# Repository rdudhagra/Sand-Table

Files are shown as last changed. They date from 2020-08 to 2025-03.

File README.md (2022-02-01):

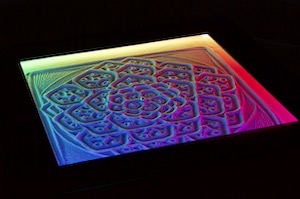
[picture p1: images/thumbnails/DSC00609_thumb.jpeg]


# Sand Table
  

### An open-source platform for building DIY sand tables (like the Sisyphus or ZenXY)
### Designed by Ravi Dudhagra ([@rdudhagra](https://github.com/rdudhagra))
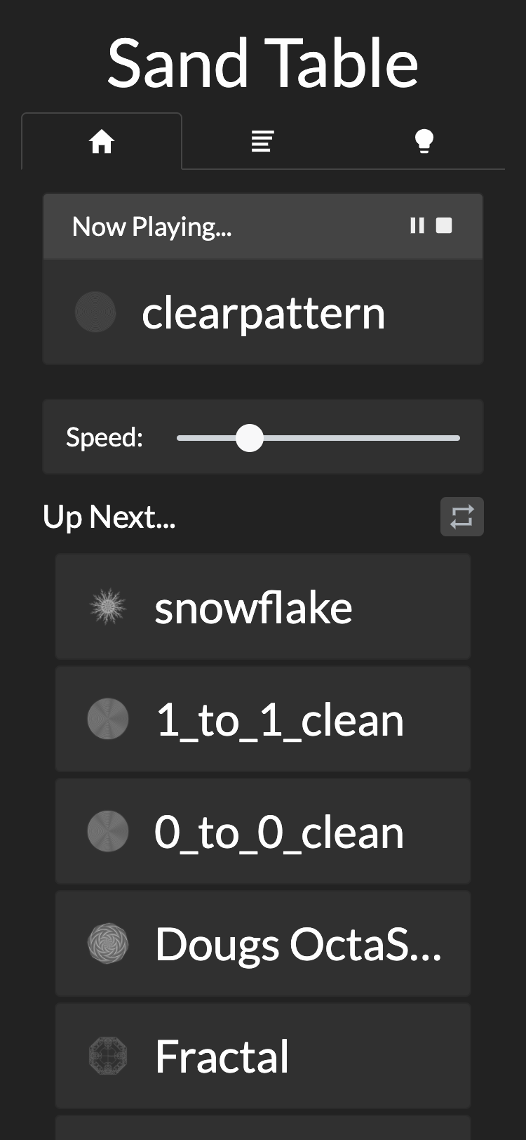
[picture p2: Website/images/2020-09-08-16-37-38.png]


Inspired by Bruce Shapiro's [Sisyphus Tables](https://sisyphus-industries.com/), I created my own DIY sand table that uses a CoreXY system to create a square-shaped canvas, yet is still fully compatible with Sisyphus Table `.thr` files. 

The table is built out of half-inch plywood and some 1x8 pine boards, glued/nailed together, and painted glossy black. The CoreXY system is built out of OpenBuilds V-Slot rail and 3D-printed parts. Use of Trinamic's TMC2209 stepper drivers means quiet movement and sensor-less homing, further simplifying the electronics under the hood. The table can be controlled directly from your smartphone thanks to a webserver that runs on an onboard Raspberry Pi. This table makes an extremely fun and rewarding project that will last a lifetime, and should cost less than $750.

See the `Build Guide` folder for instructions on my specific build, or visit the other folders for direct access to the software. Check out the `discussions` tab for other helpful info/troubleshooting advice.

> Check out [@SeanTurner71](https://github.com/SeanTurner71)'s [build video](https://www.youtube.com/watch?v=QCLmVpVkmQY) for an overview of the assembly process and some mesmerizing timelapses!

<br>

| | | |
| :---: | :---: | :---: |
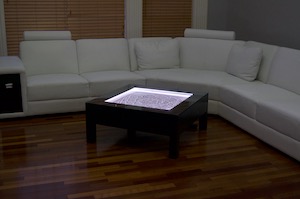
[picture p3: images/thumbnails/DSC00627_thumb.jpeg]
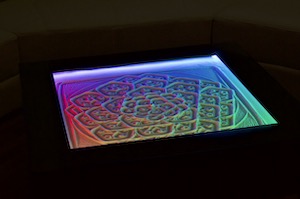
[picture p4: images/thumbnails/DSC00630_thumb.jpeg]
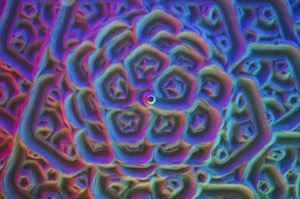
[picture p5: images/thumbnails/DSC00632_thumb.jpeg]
|  |  |  |
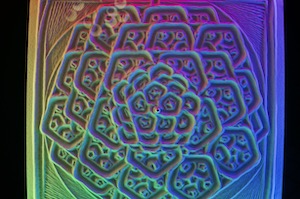
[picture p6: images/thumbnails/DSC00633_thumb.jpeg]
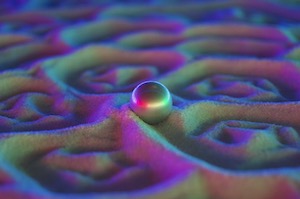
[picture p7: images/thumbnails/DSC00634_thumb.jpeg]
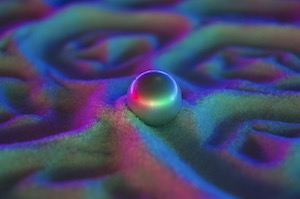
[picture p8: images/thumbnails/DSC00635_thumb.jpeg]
|  |  |  |
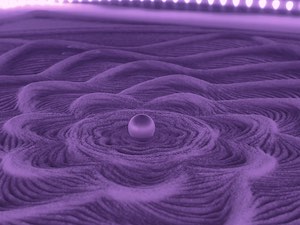
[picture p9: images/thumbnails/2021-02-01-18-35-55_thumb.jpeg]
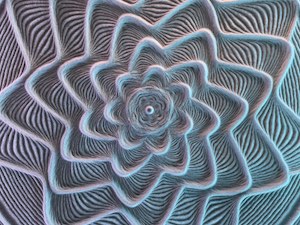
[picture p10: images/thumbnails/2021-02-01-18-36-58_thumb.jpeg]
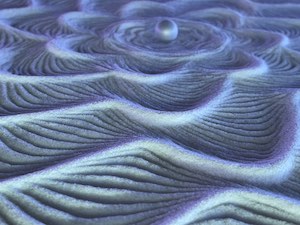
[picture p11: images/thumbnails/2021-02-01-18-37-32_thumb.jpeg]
|  |  |  |
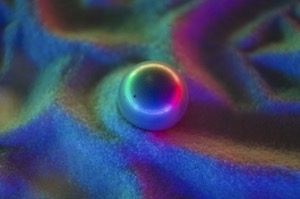
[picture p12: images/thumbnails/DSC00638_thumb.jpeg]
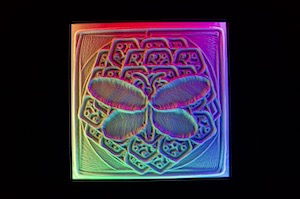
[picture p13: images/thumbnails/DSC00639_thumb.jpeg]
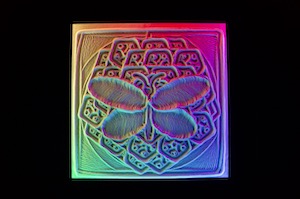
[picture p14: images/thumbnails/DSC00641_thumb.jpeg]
|  |  |  |
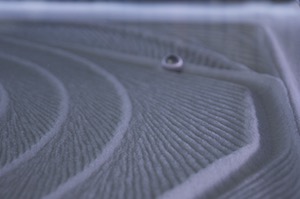
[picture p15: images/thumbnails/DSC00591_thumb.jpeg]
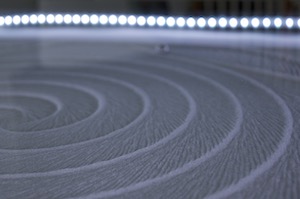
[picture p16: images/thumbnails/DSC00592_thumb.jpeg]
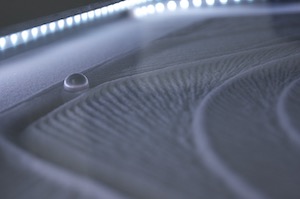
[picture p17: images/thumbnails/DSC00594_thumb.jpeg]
|  |  |  |
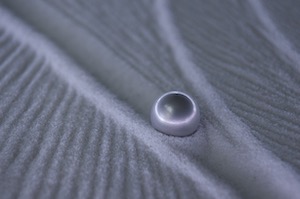
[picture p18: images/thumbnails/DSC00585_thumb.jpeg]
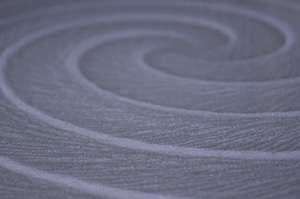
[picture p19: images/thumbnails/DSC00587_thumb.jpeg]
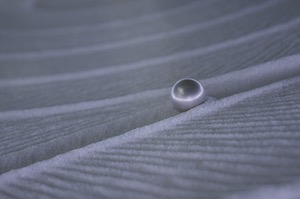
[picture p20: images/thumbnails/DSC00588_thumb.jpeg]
|  |  |  |
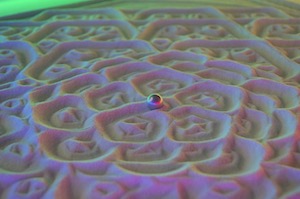
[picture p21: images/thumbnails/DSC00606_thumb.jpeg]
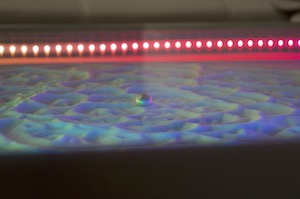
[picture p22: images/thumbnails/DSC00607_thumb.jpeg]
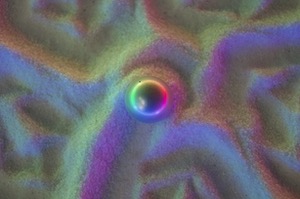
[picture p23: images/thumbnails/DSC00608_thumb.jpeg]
|  |  |  |
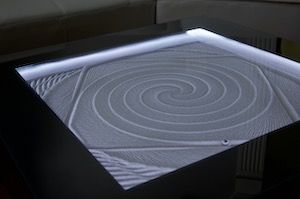
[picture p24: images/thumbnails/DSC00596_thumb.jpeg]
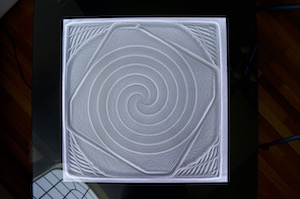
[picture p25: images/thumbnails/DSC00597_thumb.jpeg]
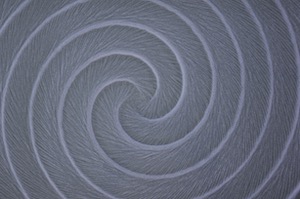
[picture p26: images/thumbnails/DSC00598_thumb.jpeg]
|  |  |  |
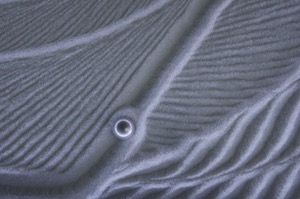
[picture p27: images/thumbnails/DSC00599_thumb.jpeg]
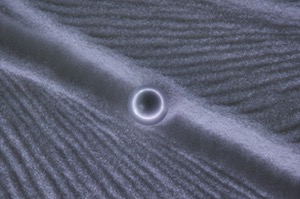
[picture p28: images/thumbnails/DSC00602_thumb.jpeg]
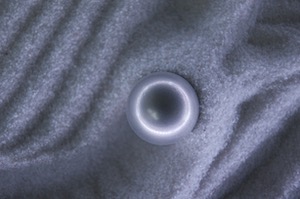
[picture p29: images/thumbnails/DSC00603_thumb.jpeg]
|  |  |  |
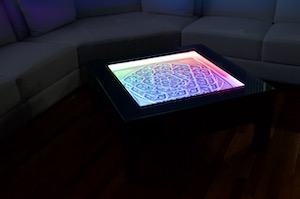
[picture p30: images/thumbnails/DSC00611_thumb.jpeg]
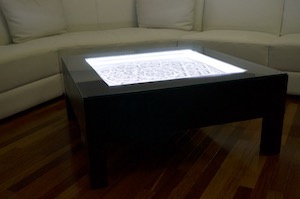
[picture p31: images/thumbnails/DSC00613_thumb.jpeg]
|  |  |  |
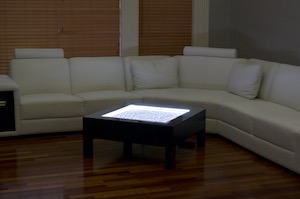
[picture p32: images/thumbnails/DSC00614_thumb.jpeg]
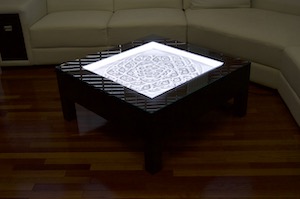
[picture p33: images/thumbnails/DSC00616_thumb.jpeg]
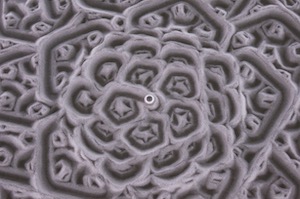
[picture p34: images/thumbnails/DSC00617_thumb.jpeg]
|  |  |  |
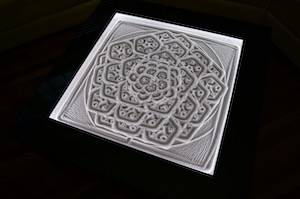
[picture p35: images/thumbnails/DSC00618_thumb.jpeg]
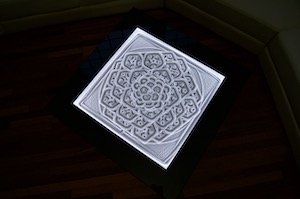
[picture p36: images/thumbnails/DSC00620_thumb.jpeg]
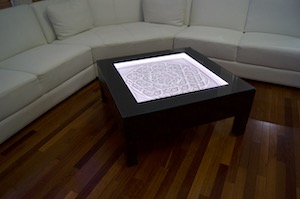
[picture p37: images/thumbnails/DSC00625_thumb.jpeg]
|  |  |  |

More pictures in the `images` folder...

<a href="https://trackgit.com">
trackgit-views
</a>

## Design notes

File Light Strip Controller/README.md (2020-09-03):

# Light Strip Controller
### An Arduino program meant for controlling an RGB LED strip using FastLED, with predefined modes and the ability to be controlled through serial
### Designed by Ravi Dudhagra ([@rdudhagra](https://github.com/rdudhagra))

## Prerequisites
Hardware:
- Arduino (literally anything that FastLED can run on...I used an Uno)
- LED Strip(s) (anything FastLED can support), and an adequate way to power them
  - Note: because of how the code was optimized to use 8-bit arithmetic (because it's orders of magnitude faster than floating-point math), this code supports **at most 255 led's**. If you want more led's, you will have to convert the 8-bit math to 16-bit/floating point arithmetic, which in that case, I would recommend using a more powerful arduino like a Due/Teensy.

## Configuration
All configuration is done in `main/constants.h`. The most important parameter is `NUM_LEDS`, which controls how many led's that the software will compute values for. 

Also important is the `DATA_PIN` parameter, which controls what pin on the Arduino will send the data to the led's. If you are using an led strip with more than one data pin (such as a DotStar), you may have to modify this file, as well as `main.ino`. 

Note that changing `FRAMES_PER_SECOND` will speed up/slow down the patterns themselves as well. 

Change `MAX_MILLIAMPS` to whatever the maximum current rating of your power source is to avoid blowing stuff up. 

The rest of the parameters control the individual modes...these can be left as is unless you're curious...

## Installing

Using the Arduino IDE (or vscode extension, etc.), upload the firmware to your Arduino. You can then use the sand table webserver to test it, or use the file `util/serial_send.py` to manually send commands.

## Development

### Creating custom modes

To create a new mode, several things must be done:
1. In `constants.h`, assign a new number to the color mode. The new number must count up from the other modes to work with the webserver (so if modes 0,1,2,3,4,5,6 are set to something, the next mode number must be 7).
2. Create a new file for your mode. Each mode contains two functions: an init function, that returns a new uint8_t* (can be used to store data about each frame like a counter, etc.), and an update function, that runs once per frame and has access to to the data pointer. See the other modes for an example.
3. In `mode.h`, update both switch statements with the new mode you just created and the functions from the new file you just created.
4. In `Website/src/app/components/Led.jsx`, add the new mode to the list `this.modes`.

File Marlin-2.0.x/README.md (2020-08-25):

# Sand Table - Customized Marlin Firmware

This is the build of Marlin that I used for my sand table build. The only modifications from stock marlin are in `configuration.h` and `configuration_adv.h`. Most of the changes fall in two categories:
- Changes everyone makes, like the dimensions of the table, steps per mm, etc.
- TMC2209-specific settings, such as microstepping and sensorless homing setup

If your sand table follows my setup exactly, this firmware should work out of the box. However, if you make modifications or want to use a newer version of Marlin, making the changes yourself should be fairly simple. Just look for a guide on setting up Marlin for a 3D-printer (but there's no z-axis or extruder, so that gets rid of 90% of the setup), and a guide for setting up the specific stepper driver you plan on using.

<br />

---

<br />
<br />
<br />

# Marlin 3D Printer Firmware






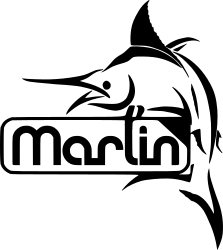
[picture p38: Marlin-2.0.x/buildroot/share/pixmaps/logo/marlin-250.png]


Additional documentation can be found at the [Marlin Home Page](http://marlinfw.org/).
Please let us know if Marlin misbehaves in any way. Volunteers are standing by!

## Marlin 2.0

Marlin 2.0 takes this popular RepRap firmware to the next level by adding support for much faster 32-bit and ARM-based boards while improving support for 8-bit AVR boards. Read about Marlin's decision to use a "Hardware Abstraction Layer" below.

Download earlier versions of Marlin on the [Releases page](https://github.com/MarlinFirmware/Marlin/releases).

## Building Marlin 2.0

To build Marlin 2.0 you'll need [Arduino IDE 1.8.8 or newer](https://www.arduino.cc/en/main/software) or [PlatformIO](http://docs.platformio.org/en/latest/ide.html#platformio-ide). Detailed build and install instructions are posted at:

  - [Installing Marlin (Arduino)](http://marlinfw.org/docs/basics/install_arduino.html)
  - [Installing Marlin (VSCode)](http://marlinfw.org/docs/basics/install_platformio_vscode.html).

### Supported Platforms

  Platform|MCU|Example Boards
  --------|---|-------
  [Arduino AVR](https://www.arduino.cc/)|ATmega|RAMPS, Melzi, RAMBo
  [Teensy++ 2.0](http://www.microchip.com/wwwproducts/en/AT90USB1286)|AT90USB1286|Printrboard
  [Arduino Due](https://www.arduino.cc/en/Guide/ArduinoDue)|SAM3X8E|RAMPS-FD, RADDS, RAMPS4DUE
  [LPC1768](http://www.nxp.com/products/microcontrollers-and-processors/arm-based-processors-and-mcus/lpc-cortex-m-mcus/lpc1700-cortex-m3/512kb-flash-64kb-sram-ethernet-usb-lqfp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)|ARM® Cortex-M3|MKS SBASE, Re-ARM, Selena Compact
  [LPC1769](https://www.nxp.com/products/processors-and-microcontrollers/arm-microcontrollers/general-purpose-mcus/lpc1700-cortex-m3/512kb-flash-64kb-sram-ethernet-usb-lqfp100-p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)|ARM® Cortex-M3|Smoothieboard, Azteeg X5 mini, TH3D EZBoard
  [STM32F103](https://www.st.com/en/microcontrollers-microprocessors/stm32f103.html)|ARM® Cortex-M3|Malyan M200, GTM32 Pro, MKS Robin, BTT SKR Mini
  [STM32F401](https://www.st.com/en/microcontrollers-microprocessors/stm32f401.html)|ARM® Cortex-M4|ARMED, Rumba32, SKR Pro, Lerdge, FYSETC S6
  [STM32F7x6](https://www.st.com/en/microcontrollers-microprocessors/stm32f7x6.html)|ARM® Cortex-M7|The Borg, RemRam V1
  [SAMD51P20A](https://www.adafruit.com/product/4064)|ARM® Cortex-M4|Adafruit Grand Central M4
  [Teensy 3.5](https://www.pjrc.com/store/teensy35.html)|ARM® Cortex-M4|
  [Teensy 3.6](https://www.pjrc.com/store/teensy36.html)|ARM® Cortex-M4|

## Submitting Changes

- Submit **Bug Fixes** as Pull Requests to the ([bugfix-2.0.x](https://github.com/MarlinFirmware/Marlin/tree/bugfix-2.0.x)) branch.
- Follow the [Coding Standards](http://marlinfw.org/docs/development/coding_standards.html) to gain points with the maintainers.
- Please submit your questions and concerns to the [Issue Queue](https://github.com/MarlinFirmware/Marlin/issues).

## Marlin Support

For best results getting help with configuration and troubleshooting, please use the following resources:

- [Marlin Documentation](http://marlinfw.org) - Official Marlin documentation
- [Marlin Discord](https://discord.gg/n5NJ59y) - Discuss issues with Marlin users and developers
- Facebook Group ["Marlin Firmware"](https://www.facebook.com/groups/1049718498464482/)
- RepRap.org [Marlin Forum](http://forums.reprap.org/list.php?415)
- [Tom's 3D Forums](https://discuss.toms3d.org/)
- Facebook Group ["Marlin Firmware for 3D Printers"](https://www.facebook.com/groups/3Dtechtalk/)
- [Marlin Configuration](https://www.youtube.com/results?search_query=marlin+configuration) on YouTube

## Credits

The current Marlin dev team consists of:

 - Scott Lahteine [[@thinkyhead](https://github.com/thinkyhead)] - USA &nbsp; [Donate](http://www.thinkyhead.com/donate-to-marlin) / Flattr: 
 - Roxanne Neufeld [[@Roxy-3D](https://github.com/Roxy-3D)] - USA
 - Chris Pepper [[@p3p](https://github.com/p3p)] - UK
 - Bob Kuhn [[@Bob-the-Kuhn](https://github.com/Bob-the-Kuhn)] - USA
 - João Brazio [[@jbrazio](https://github.com/jbrazio)] - Portugal
 - Erik van der Zalm [[@ErikZalm](https://github.com/ErikZalm)] - Netherlands &nbsp; 

## License

Marlin is published under the [GPL license](/LICENSE) because we believe in open development. The GPL comes with both rights and obligations. Whether you use Marlin firmware as the driver for your open or closed-source product, you must keep Marlin open, and you must provide your compatible Marlin source code to end users upon request. The most straightforward way to comply with the Marlin license is to make a fork of Marlin on Github, perform your modifications, and direct users to your modified fork.

While we can't prevent the use of this code in products (3D printers, CNC, etc.) that are closed source or crippled by a patent, we would prefer that you choose another firmware or, better yet, make your own.

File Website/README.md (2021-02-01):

<h1>Webserver</h1>
<h3>A NodeJS webserver with ReactJS and Bootstrap for controlling your sand table remotely</h3>

Designed by Ravi Dudhagra ([@rdudhagra](https://github.com/rdudhagra))

- [Installation Instructions](#installation-instructions)
  - [Prerequisites](#prerequisites)
  - [Building](#building)
  - [Running the webserver](#running-the-webserver)
  - [Running the webserver (development)](#running-the-webserver-development)
- [Downloading tracks](#downloading-tracks)
- [Screenshots](#screenshots)

# Installation Instructions

## Prerequisites
This project was developed with the following:
- `NodeJS v13.11.0`
- `NPM v6.14.5`

## Building
1. Download this folder to the directory of choice
2. In the same directory as `package.json`, run
   ```bash
   npm install # installs packages and dependencies
   ```
3. In the file `.env`, edit the parameters to match your setup

## Running the webserver
1. In the same directory as `package.json`, run
   ```bash
   npm run prod # compiles client and server files in production mode, and runs server
   ```
2. Visit `http://[ip address of machine]` in a web browser (runs on port 80)

If you want to run this webserver through systemd, the script `start.sh` should assist in this, assuming you're using NVM to manage Node versions.

## Running the webserver (development)
1. In the same directory as `package.json`, run
   ```bash
   npm start # compiles client files, compiles server files in memory, starts server with nodemon (restarts on file changes)
   ```
2. Visit `http://[ip address of machine]:3000` in a web browser (runs on port 3000)

# Downloading tracks
Any `.thr` file compatible with the Sisyphus table will work with this software. A collection of publicly available tracks can be found at the following links:
- https://github.com/Dithermaster/sisyphus
- https://github.com/SlightlyLoony/JSisyphus
- https://github.com/heropup/sisyphus
- http://thejuggler.net/sisyphus/
- https://github.com/ddkengr/Sisyphus-threads

# Screenshots

| | | |
| :---: | :---: | :---: |
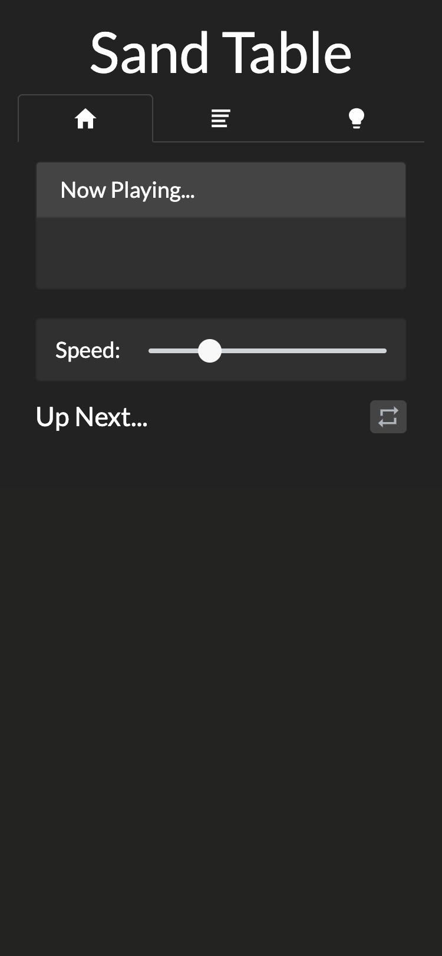
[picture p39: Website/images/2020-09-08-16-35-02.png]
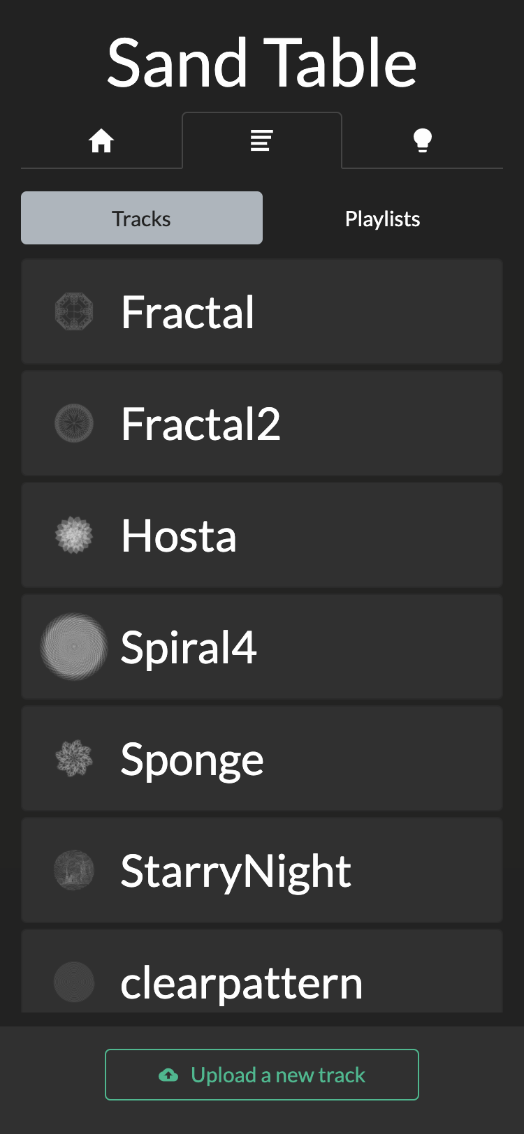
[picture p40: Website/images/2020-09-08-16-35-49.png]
|  |  |  |
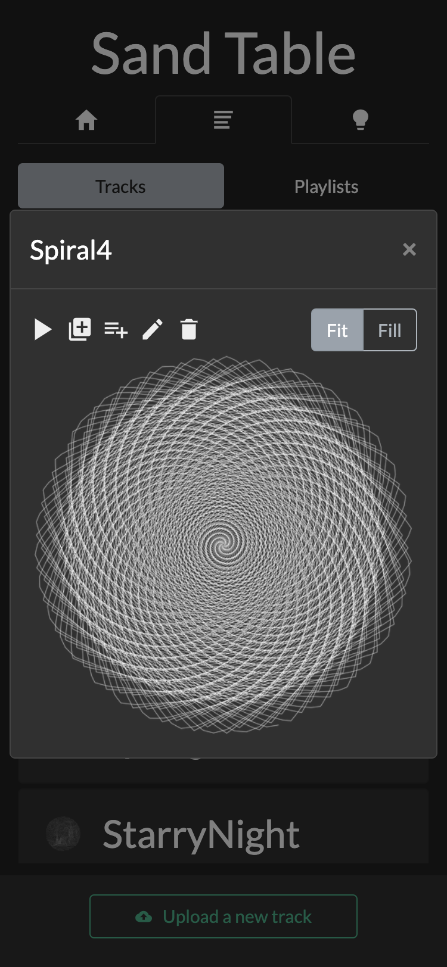
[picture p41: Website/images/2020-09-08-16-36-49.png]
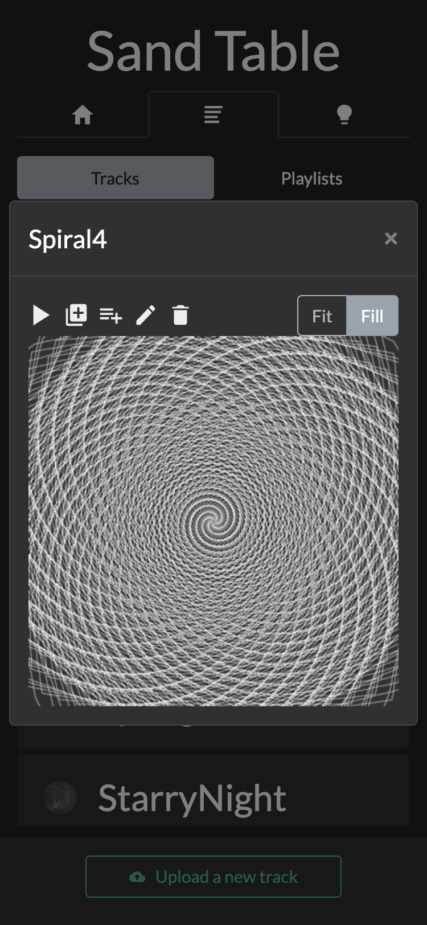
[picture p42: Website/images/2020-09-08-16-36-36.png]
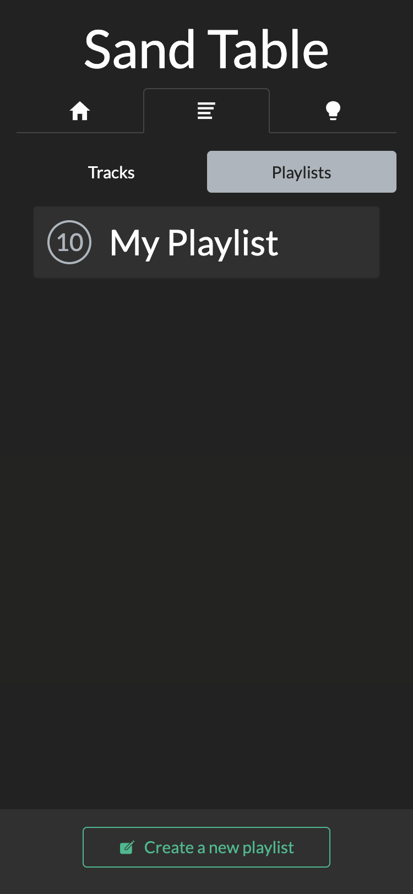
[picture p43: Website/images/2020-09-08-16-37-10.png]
|  |  |  |
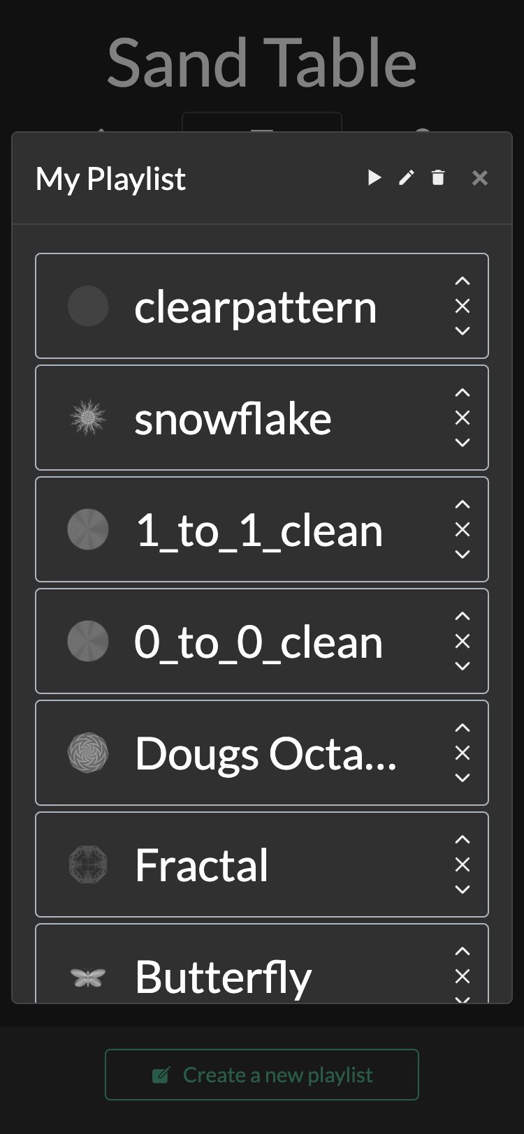
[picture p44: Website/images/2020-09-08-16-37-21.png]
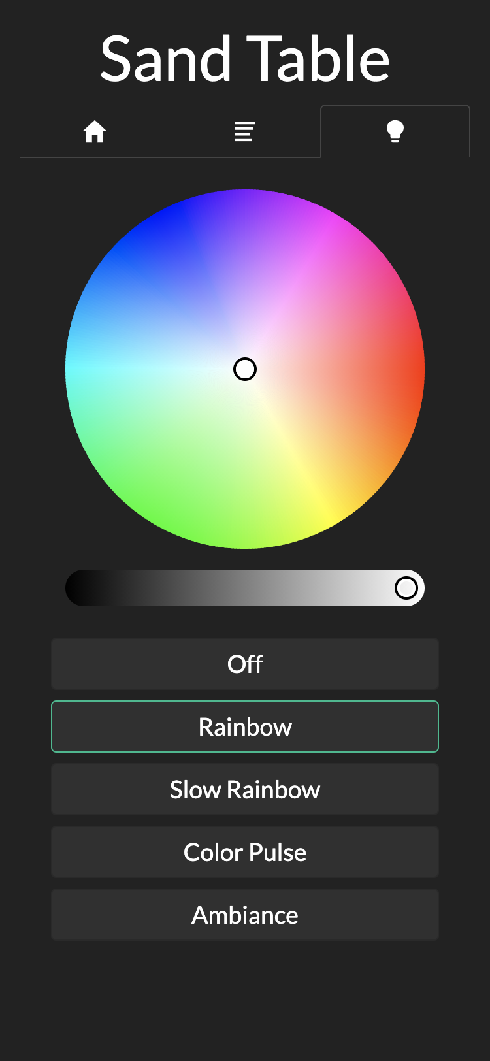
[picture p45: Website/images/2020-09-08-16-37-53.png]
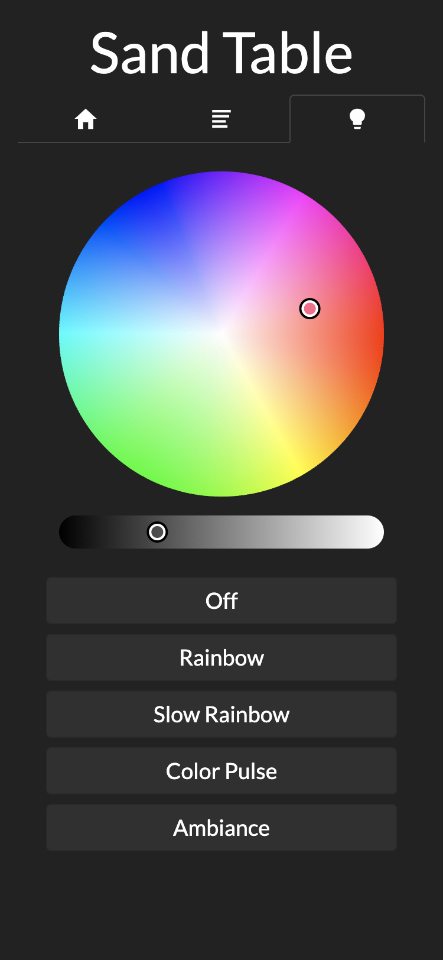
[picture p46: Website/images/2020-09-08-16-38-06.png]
|  |  |  |

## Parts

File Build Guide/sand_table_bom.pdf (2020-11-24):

Item | Link | Price | Quantity | Total | Remarks
| 1x8 pine board (8'), square edges | https://www.homedepot.com/p/1-in-x-8-in-x-8-ft-Select-Pine-Board-929612/202535862 $ | 22.22 | 2 | $ 44.44 | If you have proper woodworking tools, you could probably get away with lower-quality boards
| 1/2" sanded plywood, 4'x8' | https:/ /www.homedepot.com/ p/ 12mm-Sande-Plywood-1-2-in-Category-x-4-ft-x-8-ft-Actual-0-472-in-x-48-in-x-96-in-454532/ 203414055 | $ 35.95 | 1 | $ 35.95
| 5.0mm underlayment plywood, 4'x4' | https:/ /www.homedepot.com/ p/Tri-PLY-U nderlayment-Common-5-0-mm-x-4-ft-x-4-ft-Actual-0-196-in-x-47-75-in-x-48-in-448887/ 202327787 | $ 10.48 | 1 | $ 10.48 | Any thin wood will work, this is a pretty economical choice
| Finishing nails | https://www.homedepot.com/p/Grip-Rite-13-x-2-in-6-Penny-Bright-Steel-Finish-Nails-1-lb-Pack-6F1/100027781 | $ 4.75 | 1 | $ 4.75
| Gray spray paint primer | https:/ /www.homedepot.com/ p/ Rus t-Oleum-Painter-s -Touch-2X-12-oz -Flat-G ray-Primer-General-Purpose-Spray-Paint-334017/ 307244825 | $ 3.98 | 6 | $ 23.88 | You'll need more than you think
| Gloss black spray paint | https://www.homedepot.com/p/Rust-Oleum-Painter-s-Touch-2X -12 -oz-Gloss-Black-General-Purpose-Spray-Paint-334026/307244831 | $ 3.98 | 4 | $ 15.92 | These are probably not the best options…but choose whatever you need for the finish that you want to achieve
| Clear coat spray paint | https://www.homedepot.com/p/Rust-Oleum-Painter-s-Touch-2X -12 -oz-Gloss-Clear-General-Purpose-Spray-Paint-334029/307244797 | $ 3.98 | 1 | $ 3.98 | Makes the finish slightly less glossy, but improves durability
| M8 Nuts | https://www.homedepot.com/p/Everbilt-M8-10-9-Zinc-Metric-Hex-Nut-5-per-Bag-802418/204281770 | $ 2.27 | 1 | $ 2.27 | For use with the IKEA legs
M8 Washers | https://www.homedepot.com/p/Everbilt-M8-Zinc -Plated-Metric -Flat-Washer-5-Piece-Bag-802458/204604800 | $ 0.97 | 1 | $ 0.97 | Or whatever you can find in your spare parts drawer that's close enough
BRENNÅSEN bed legs (IKEA) | https://www.ikea.com/us/en/p/brennasen-leg-black-stained-00299689/ | $ 30.00 | 1 | $ 30.00 | Not always in stock, but alternatives either have long shipping times or are pricey (or you could make your own legs…)
36"x36" Glass table top (1/4" thick) | h ttp s://www.amazo n .co m/Sq u are-Glass-Tab le-Th ick-P o li sh ed /d p /B 0 0 1 E6 C ZKW /ref=sr_1 _7 ?crid =2 R ZX DC HGC K 6 X 5 &d ch ild =1 &keywo rd s=3 6 x3 6 +glass+tab le+to p &q id =1 5 9 8 9 0 2 6 4 3 &sp refix=3 6 x3 6 +glass+tab le%2 C ap s%2 C 1 3 7 &sr=8 -7 | $ 99.95 | 1 | $ 99.95 | You should check the availability of local glass suppliers in your area for a better deal (I purchased mine for around $60)
| 3D Printer Filament (PLA) | https://www.amazon.com/HATCHBOX-3D-Filament-Dimensional-Accuracy/dp/B00J0ECR5I?ref_=ast_sto_dp | $ 22.99 | 1 | $ 22.99 | Whatever you have will work, but you'll need the majority of the spool for all the parts. If you can print with something stronger like PETG, that's better.
| Stepper motor dampers | https://www.amazon.com/gp/product/B07GWN6V89/ref=ppx_yo_dt_b_asin_title_o08_s00?ie=UTF8&psc=1 | $ 13.99 | 1 | $ 13.99 | Not required, but greatly reduce noise
| M5 Square nuts | https://www.amazon.com/gp/product/B01HSKL7Z6/ref=ppx_yo_dt_b_asin_title_o03_s00?ie=UTF8&psc=1 | $ 8.09 | 1 | $ 8.09 | You won't need this many
| 12V to 5V step-down, 15A max | https://www.amazon.com/gp/product/B07V7YY5X6/ref=ppx_yo_dt_b_asin_title_o05_s00?ie=UTF8&psc=1 | $ 13.95 | 1 | $ 13.95
| M5 10mm bolts | https://www.amazon.com/gp/product/B07KWQ4JFK/ref=ppx_yo_dt_b_search_asin_title?ie=UTF8&psc=1 | $ 8.49 | 1 | $ 8.49
| M5 40mm bolts | https://www.amazon.com/gp/product/B083F9MVWT/ref=ppx_yo_dt_b_asin_title_o07_s00?ie=UTF8&psc=1 | $ 8.99 | 1 | $ 8.99
| TMC2209 Stepper drivers | https://www.amazon.com/gp/product/B07W5S3KVF/ref=ppx_yo_dt_b_asin_title_o07_s02?ie=UTF8&psc=1 | $ 29.98 | 1 | $ 29.98 | You only need two, this comes with four
| 1 kOhm resistors | https:/ /www.amazon.com/ Projects -100EP5141K00-Ohm-Resis tors -Pack/ dp/ B0185FGTSS/ ref=s r_1_9?dchild=1&keywords=1k+ohm+resis tor&qid=1598903733&s=indus trial&s r=1-9 | $ 5.82 | 1 | $ 5.82 | You only need two, this comes with 100
| Jumper Wires | ht t ps: / /www. am azon. com /Elegoo- EL - CP- 004- M ult icolor ed- Br eadboar d- ar duino/ dp/ B01EV70C78/ r ef =s r _1_5?cr id=34B0X8G6A3496&dchild=1&keywor ds=jum per +cables+f em ale+t o+f em ale&qid=1598906507&s pr ef ix=jum per +cables+f em al+%2Caps%2C134&s r =8- 5 | $ 6.98 | 1 | $ 6.98 | You only need three female-to-female cables that you'll have to cut and splice, so if you have that or have the materials to crimp your own wires, this isn't necessary
| Power wire | https:/ /www.amazon.com/TYUMEN -Hookup-Electrical-Strips -Extension/ dp/ B07SJ44SN 1/ ref=s r_1_7?dchild=1&keywords=20+gauge+wire&qid=1598906583&s r=8-7 | $ 15.99 | 1 | $ 15.99 | Stranded is best, but if you have solid-core wire on hand, that will work as well (that's what I did)
| NEMA17 Steppers | https://www.amazon.com/gp/product/B00PNEQI7W/ref=ppx_yo_dt_b_asin_title_o07_s03?ie=UTF8&psc=1 | $ 12.99 | 2 | $ 25.98 | These have long cables already soldered with female connectors. If you get steppers from somewhere else, you may have to solder connectors yourself.
| 12V 10A power supply | https://www.amazon.com/gp/product/B00Z9X4GLW/ref=ppx_yo_dt_b_asin_title_o07_s03?ie=UTF8&psc=1 | $ 19.99 | 1 | $ 19.99
| F623ZZ Bearings | https://www.amazon.com/gp/product/B07MGTM2L4/ref=ppx_yo_dt_b_asin_title_o07_s05?ie=UTF8&psc=1 | $ 8.48 | 2 | $ 16.96
| GT2 Belt - 10m | https:/ /www.amazon.com/Mercurry-Meters -timing-Ros tock-GT2-6mm/ dp/ B01E91K4N 8/ ref=s r_1_3?dchild=1&keywords=10m+gt2+belt&qid=1598908569&s=indus trial&s r=1-3 | $ 10.99 | 1 | $ 10.99
| Mini V-Wheels (off-brand) | https://www.amazon.com/gp/product/B07V4GHLL8/ref=ppx_yo_dt_b_asin_title_o07_s06?ie=UTF8&psc=1 | $ 9.99 | 2 | $ 19.98
| 16 teeth GT2 pulleys | https://www.amazon.com/gp/product/B07DBN8KFT/ref=ppx_yo_dt_b_asin_title_o07_s06?ie=UTF8&psc=1 | $ 7.96 | 1 | $ 7.96
| RAMPS 1.6+ board | https://www.amazon.com/gp/product/B07RF576WC/ref=ppx_yo_dt_b_asin_title_o07_s06?ie=UTF8&psc=1 | $ 12.99 | 1 | $ 12.99 | Any RAMPS board will work

# Sand Table Bill of Materials

# By Ravi Dudhagra (https://github.com/rdudhagra/Sand-Table)

# Table Hardware

Arduino MEGA 2560 | https:/ /www.amazon.com/ELEGOO -ATmega2560-ATMEG A16U 2-Projects -Compliant/ dp/ B01H4ZLZLQ/ ref=s r_1_3?dchild=1&keywords=arduino+mega&qid=1598908682&s r=8-3 | $ 15.99 | 1 | $ 15.99 | You could replace this and the RAMPS board with a single board such as the SKR 1.3…I had the MEGA already, so the RAMPS was the best option for me.
Assorted M3 Screws | https://www.amazon.com/gp/product/B08125LTBT/ref=ppx_yo_dt_b_asin_title_o07_s07?ie=UTF8&psc=1 | $ 25.98 | 1 | $ 25.98 | You need 5% of the screws in this pack, but it's a good deal
M5 Washers | https://www.amazon.com/gp/product/B009OK4TZO/ref=ppx_yo_dt_b_asin_title_o07_s08?ie=UTF8&psc=1 | $ 3.66 | 1 | $ 3.66
M5 Nylock Nuts | https://www.amazon.com/gp/product/B0761189F5/ref=ppx_yo_dt_b_asin_title_o07_s08?ie=UTF8&psc=1 | $ 5.64 | 1 | $ 5.64
Raspberry Pi | https://www.adafruit.com/product/4295 | $ 30.00 | 1 | $ 30.00 | A Model 3B+ (what I used) or newer will work, this is the cheapest one I could find (Pi 4 Model B 1GB).
Micro SD Card | h ttp s://www.amazo n .co m/San d i sk-Ul tra-M icro -UHS-I -Ad ap ter/d p /B 0 7 3 K 1 4 C VB /ref=sr_1 _3 ?crid =3 FTB 5 RGA6 QLN5 &d ch ild =1 &keywo rd s=8 gb +micro +sd +card &q id =1 5 9 8 9 0 9 1 2 0 &sp refix=8 gb +micro %2 C ap s%2 C 2 2 7 &sr=8 -3 | $ 6.19 | 1 | $ 6.19 | Anything of acceptable quality should be fine…
LED Strips (4m) | h ttp s://www.amazo n .co m/Ligh t-Ad d ressab le-WS2 8 1 2 -Waterp ro o f-3 M eter/d p /B 0 8 7 B 5 R P LK /ref=sr_1 _5 ?d ch ild =1 &keywo rd s=led %2 B strip %2 B 4 m%2 B ws2 8 1 2 &q id =1 5 9 8 9 0 9 3 8 5 &sr=8 -5 &th =1 | $ 24.99 | 1 | $ 24.99 | Go for whatever you are comfortable with. These are a good price and should work. I used something a bit more pricey since I had some on-hand (https://www.mouser.com/ProductDetail/Seeed-Studio/104020109?qs=byeeYqUIh0PmEriTC2u0yQ%3D%3D, Qty 4)
Openbuilds V-Slot Linear Rail (1500mm) | http://makerstore.cc/product/v-slot-20-x-40mm/ | $ 20.90 | 2 | $ 41.80 | There are many other places that sell this…look for one that's on sale (when I bought mine makerstore was 30% off)
1" Cube Neodynium Magnet | https:/ /www.amazon.com/ CMS-Magnetics -G rade-Neodymium-Magnet/ dp/ B008D3N XQO/ ref=s r_1_12?dchild=1&keywords=1+in+cube+neodymium+magnet&qid=1599060210&s r=8-12 | $ 12.98 | 1 | $ 12.98
Arduino Uno (or any other arduino) | https:/ /www.amazon.com/ELEGOO -Board-ATmega328P-ATMEG A16U 2-Compliant/ dp/ B01EWOE0UU / ref=s r_1_4?dchild=1&keywords=arduino+cheap&qid=1598909615&s r=8-4 | $ 12.98 | 1 | $ 12.98 | Any Arduino that can run LED strips will work (specifically can run the FastLED library)
| Sand | https:/ /www.amazon.com/ Bulk-W hite-Fine-Sand-lbs / dp/ B078YCRCQP/ ref=s r_1_2?dchild=1&keywords=fun+expres s+sand+white&qid=1598909975&s r=8-2 | $ 14.99 | 2 | $ 29.98 | I found this to work well. It's fine, but not too fine to the point where it's just a powder
| Assorted Sandpaper | https:/ /www.amazon.com/ 24PCS-Variety-Sandpaper-As s orted-Sanding/ dp/ B07R64PZ8N / ref=s r_1_5?dchild=1&keywords=sandpaper&qid=1598910485&s r=8-5 | $ 5.99 | 1 | $ 5.99 | Amazon sandpaper isn't terrible
| Wood glue | https://www.homedepot.com/p/Titebond-II-16-oz-Premium-Wood-Glue-5004/100144210 | $ 5.97 | 1 | $ 5.97 | Any wood glue will work
Hardware | $ 272.59
Electronics | $ 430.33
Miscellaneous | $ 41.94
Total | $ 744.86

# Electronics Misc

36%

58%

6%

# Hardware Electronics Miscellaneous

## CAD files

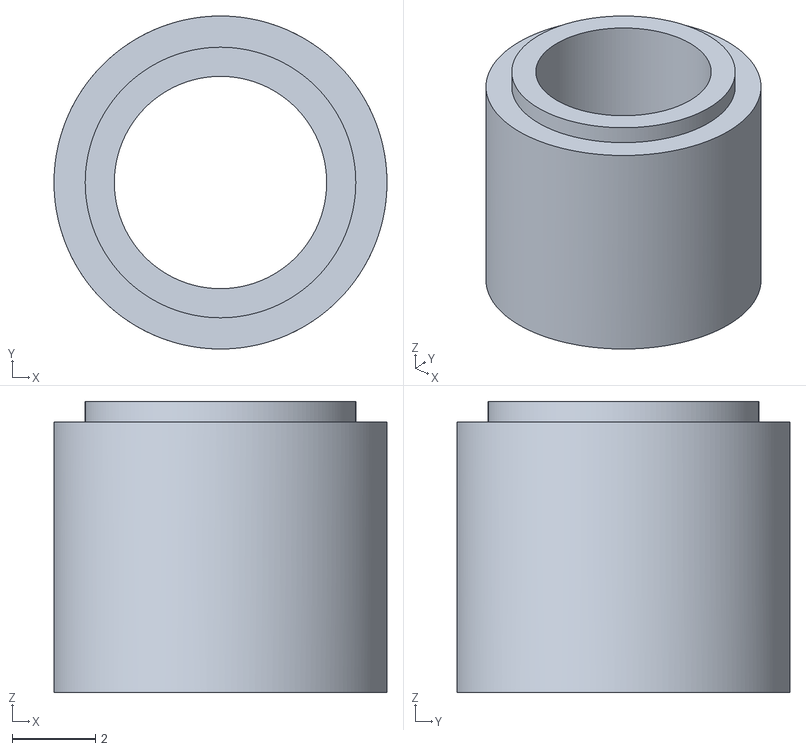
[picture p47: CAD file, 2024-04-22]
Build Guide/STLs/24-WheelSpacer.stl
8.00 x 8.00 x 7.00

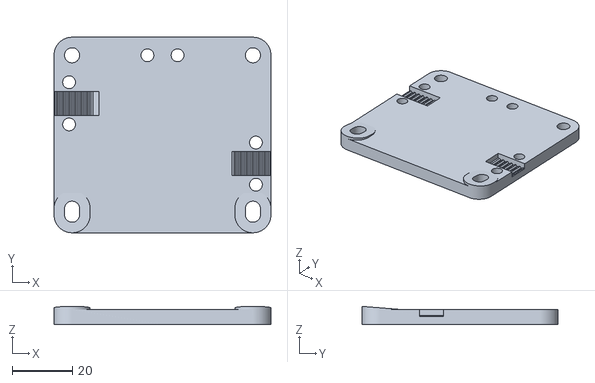
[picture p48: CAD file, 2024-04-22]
Build Guide/STLs/Alternate Parts/2-PrintCarriageFront_HeatSetInserts.stl
72.0 x 64.9 x 6.06

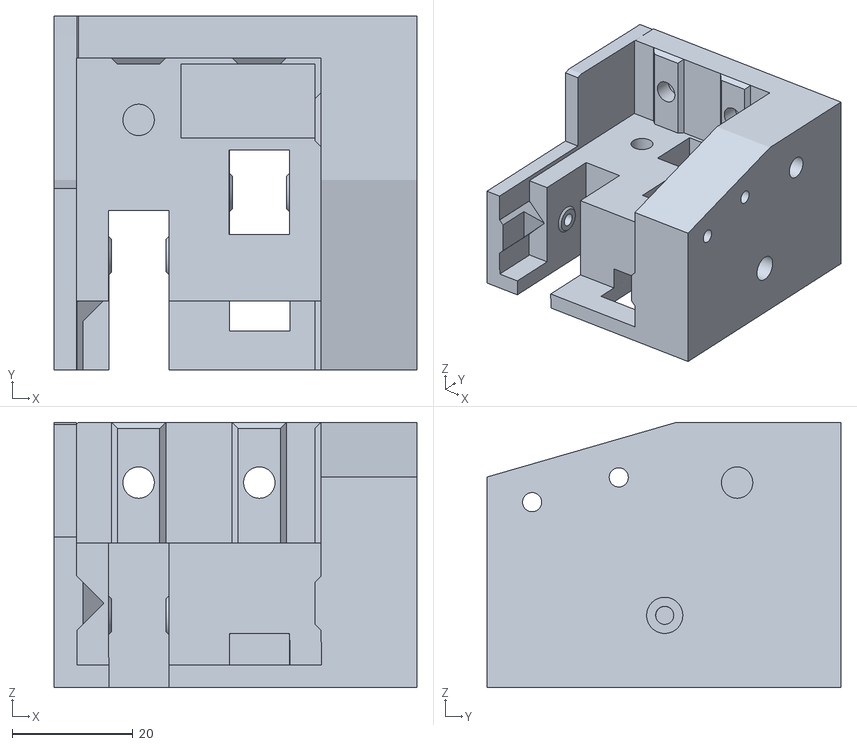
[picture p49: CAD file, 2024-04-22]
Build Guide/STLs/Alternate Parts/1-RearIdlerLeft_NoRearBar.stl
60.2 x 58.6 x 44.0

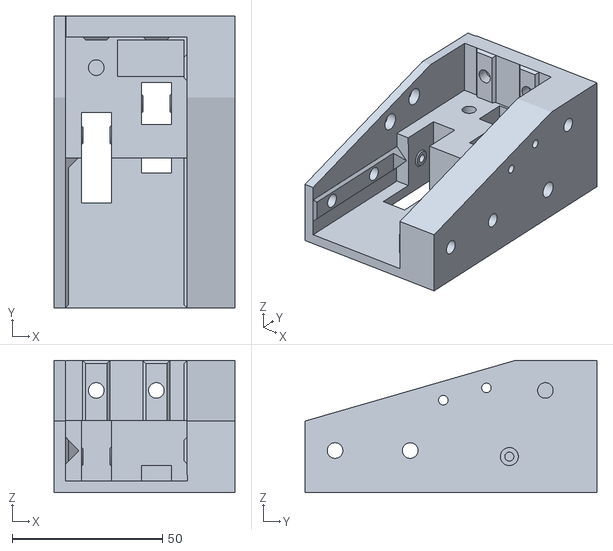
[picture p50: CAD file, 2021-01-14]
Build Guide/STLs/1-RearIdlerLeft.stl
60.2 x 97.2 x 44.0

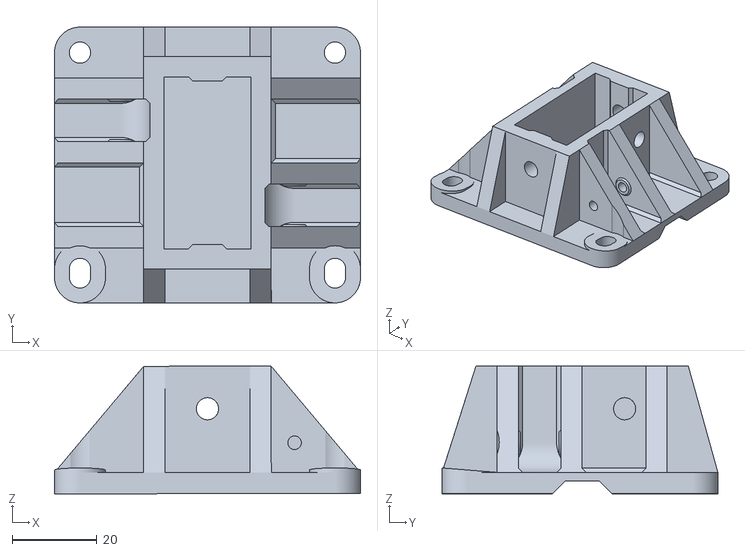
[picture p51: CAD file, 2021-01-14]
Build Guide/STLs/2-HbarEnd.stl
72.0 x 64.9 x 30.0

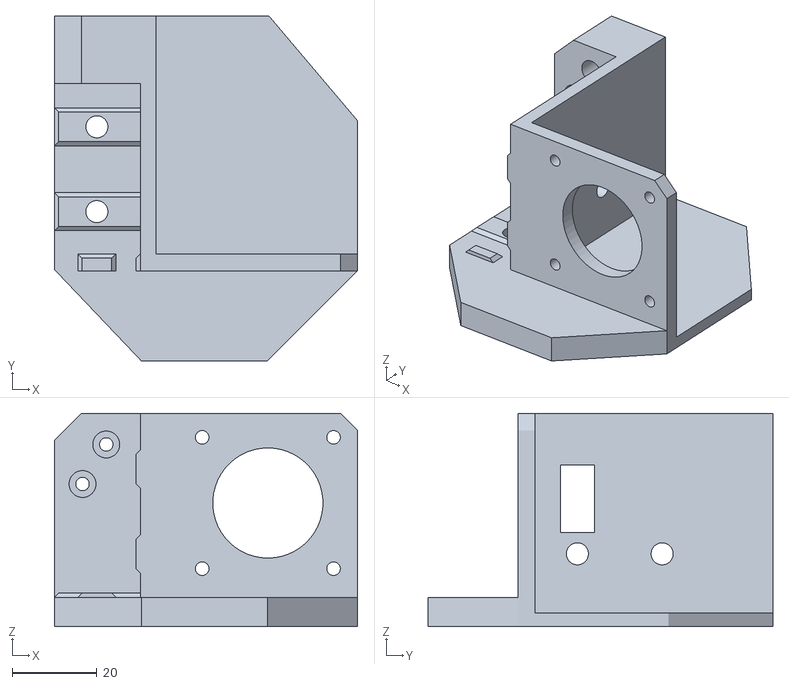
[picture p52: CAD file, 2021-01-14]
Build Guide/STLs/1-MotorMountRight.stl
71.5 x 81.4 x 50.3

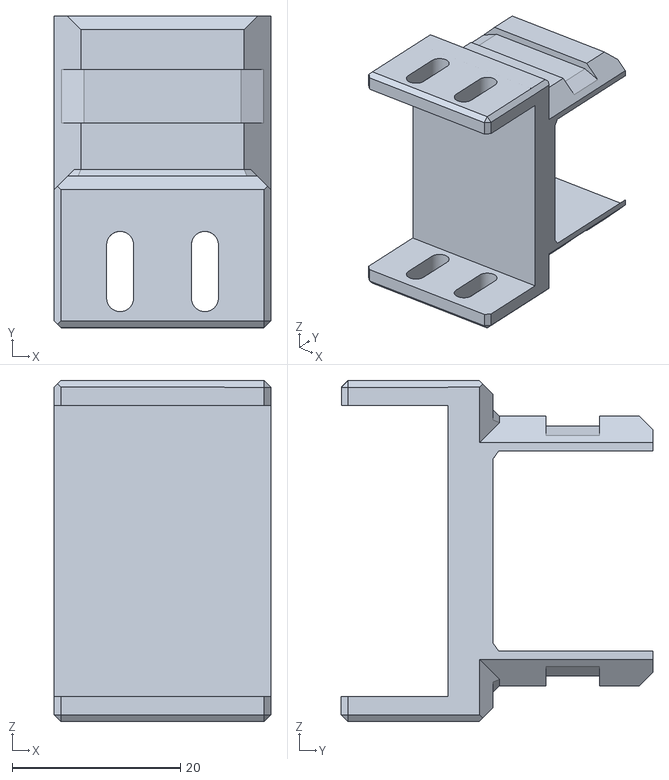
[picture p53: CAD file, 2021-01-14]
Build Guide/STLs/1-MagnetClamp.stl
25.8 x 37.1 x 40.6

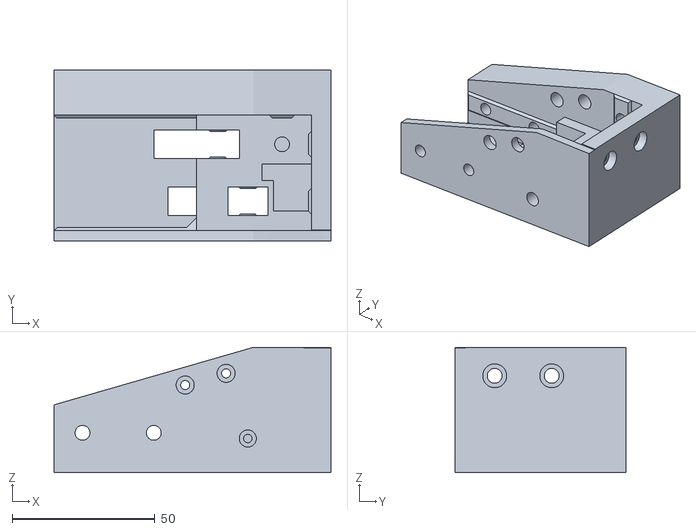
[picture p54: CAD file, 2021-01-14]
Build Guide/STLs/1-RearIdlerRight.stl
97.2 x 60.1 x 44.0

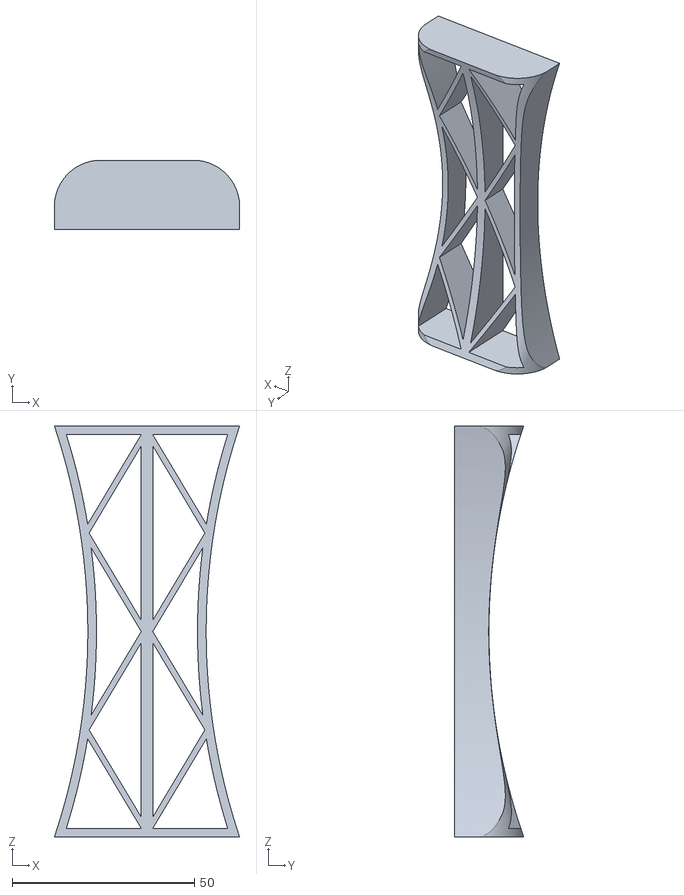
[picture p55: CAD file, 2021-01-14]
Build Guide/STLs/4-Riser.stl
50.8 x 19.0 x 112.7

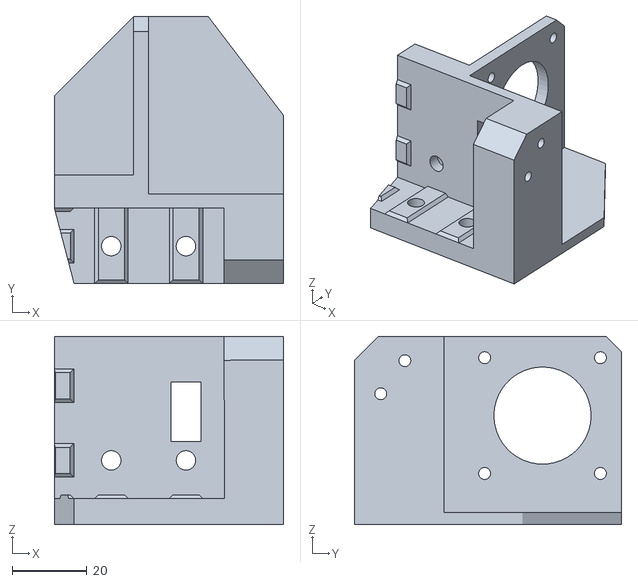
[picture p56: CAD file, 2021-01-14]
Build Guide/STLs/1-MotorMountLeft.stl
61.4 x 71.5 x 50.4

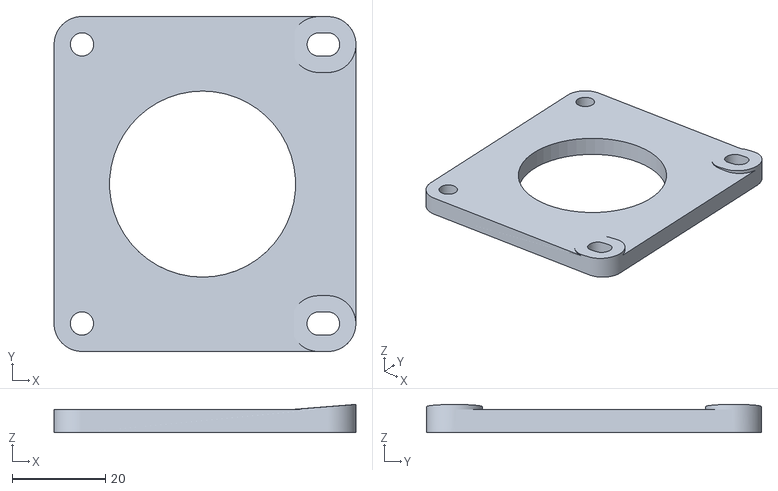
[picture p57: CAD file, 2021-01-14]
Build Guide/STLs/2-HbarEndPlate.stl
64.9 x 72.0 x 6.08

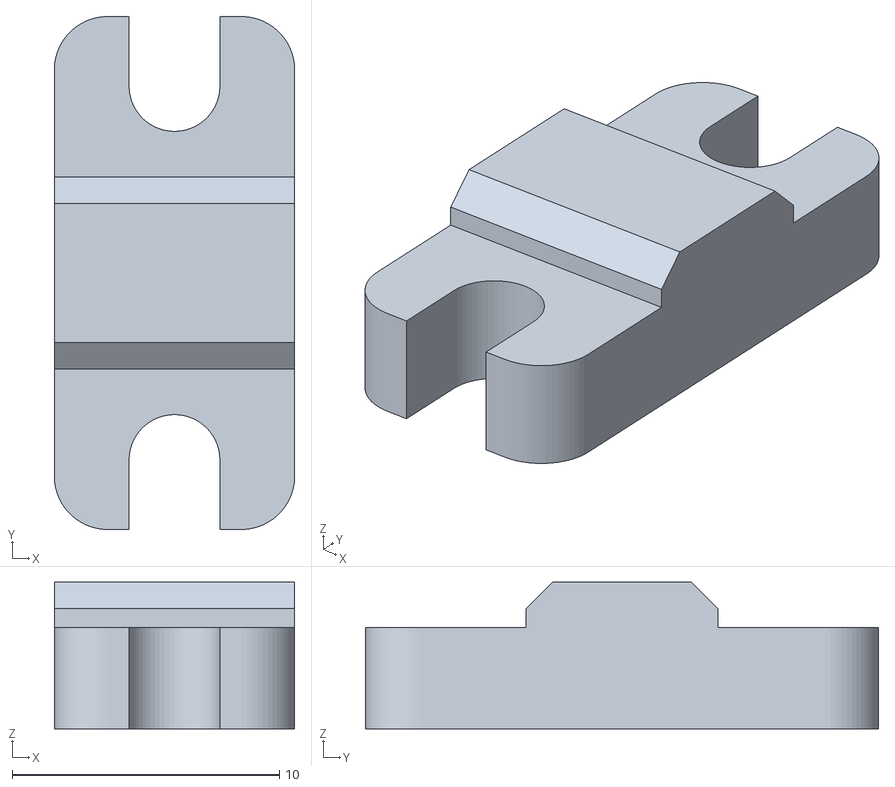
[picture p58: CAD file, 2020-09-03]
Build Guide/STLs/4-BeltClamp.stl
9.00 x 19.2 x 5.50

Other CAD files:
Build Guide/STLs/2-PrintCarriage.stl
Build Guide/STLs/Alternate Parts/1-RearIdlerRight_NoRearBar.stl

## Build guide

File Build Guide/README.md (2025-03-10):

# Sand Table Build Guide

### Designed by Ravi Dudhagra ([@rdudhagra](https://github.com/rdudhagra))

This is a build guide for those who want to construct a table similar to mine. The end result will be a 3'x3' coffee table, 16" high.

## Prerequisites

While everything for the table itself is included in the BOM, a few tools are required (all should be available at a local makerspace):

- Drill and assorted drill bits (mostly small, but you'll need something around 1" for the power cord hole)
- Screwdriver with metric hex bits
- Pliers/wrench for holding nuts in place
- Hammer for the finishing nails (or a hard, heavy object)
- 3D Printer
- Soldering iron and solder (access to heat-shrink tubing is also nice)
- Saw capable of long, straight cuts, like a table saw/circular saw/large bandsaw
- Miter saw capable of 45 degree miters
- Some clamps (not required but extremely helpful for the glue-ups)
- **Proper safety gear**

## Bill Of Materials

See `sand_table_bom.pdf` or `sand_table_bom.xlsx` for a bill of materials. I put everything I could think of on the list...chances are that you have at least some of the items already, and the worst case is that you'll have a lot of extra parts for your next project!

## CAD Model

In case the below steps weren't clear, or if you want to modify the design yourself, you can find the CAD model of the entire table at https://a360.co/2QLgInO, and just the CoreXY gantry at https://a360.co/31KW79k.

## Building the actual table

Assembly of the table is straightforward; you only need basic woodworking skills and the knowledge (or someone else with the knowledge) of how to safely operate the power tools required.

See `Assembly Guide.pdf` for diagrams of all the cuts and the assembly.

### Board sizes to cut

1. Four 1x8 boards, 36 inches long, with the edges mitered at 45 degrees (the long side is 36"). The boards should form the walls of the table when put together.
2. A 1/2" plywood board, measuring 34.5" square
3. A 1/2" plywood board, measuring 33.875" square
4. Two plywood strips (cut from the underlayment plywood board in the BOM or another thin wood sheet), measuring 33.875" long and 2" high
5. Two plywood strips (cut from the underlayment plywood board in the BOM or another thin wood sheet), measuring 33.875" + 2 times the width of the wood sheet you're using, and 2" high
6. Four plywood strips, 36" long, 5" high, and mitered at 45 degrees

### Assembly (before paint)

1. Glue the four 1x8 boards together into a frame with the bottom board (the larger plywood square). This should form a shallow box with no top. If needed, finishing nails/clamps can be used to hold the parts together while drying.
2. Glue the top board (smaller plywood square) to the plywood strips (that are 2" high) to form another shallow box (more like a tray than a box). Make sure that seams are sealed with glue or something else, so that sand cannot go through the cracks and mess up the electronics.
3. Glue the remaining plywood strips (5" high) into a ring. Make sure that the strips are aligned vertically; this will reduce the amount of work you'll have to do later when sanding.
4. You can fill in any cracks with some wood filler or wood glue and then sand flat

### Sanding/Painting

I wanted to achieve a smooth, glossy black finish for my table. Here are the steps I took:

1. First, sand all surfaces smooth. I used 60/120 grit sandpaper on my sheet sander to get rid of bumps and level everything out, then worked my way up to 240 grit and then 400 grit on all surfaces.
2. I then used spray paint primer and laid a thick coat on all surfaces. I sanded everything at 400 grit until smooth (without sanding all the paint away), and added another coat of primer on all surfaces, and sanded again at 400 grit.
3. On surfaces that were not going to be seen when the table is assembled (like inside walls and the bottom, etc.), I stopped here. On outside surfaces, I applied coats of primer and wet-sanded consecutively at 800 and 1200 grits. At these higher grits, I sanded by hand rather than with the sheet sander.
4. Last, I applied coats of black glossy paint on all surfaces, and then applied a coat of clear-coat on the outside surfaces to protect the paint.

This process seems simple when written out, but take your time sanding, especially early-on, otherwise any defects will be seen on the final coats.

### Assembly (after paint)

1. Install the legs on the four corners of the table by drilling a hole for the center screw and then tightening a nut/washer from the inside. Take care to ensure that the legs are flush with the end of the table for a polished look.
2. Cut a hole for the power wire along one of the edges, near the left corner (see later in this guide for some context on where the hole should go).

## Building the gantry

The gantry design was heavily influenced by the [D-Bot CoreXY 3D Printer](https://www.thingiverse.com/thing:1001065). Essentially, I took the top gantry of the 3D printer and modified it to work with the sand table. I highly recommend looking at their build guide (a copy can be found here as well) for how to assemble the gantry, as it is quite similar and is documented far-better.

1. Print all parts in the `STLs` folder. The number at the beginning of each part's filename indicates how many you will need. These parts should be printed solid, or at least with a lot of shells.
2. You will need to make two cuts in your VSlot extrusions. These lengths assume that your two extrusions are 1500mm long. The first extrusion should be cut into two pieces of equal length, and will be referred to as the _side rails_. The second extrusion needs to be cut into two pieces such that one of the pieces is 25mm longer than the other. The longer piece will be the _hbar rail_, and the shorter piece will be the _back rail_. Be sure to account for the thickness of your saw blade when you cut your pieces.
3. Install the bearings on the rear idlers and hbar end idlers, per the D-bot build guide pdf pages 11-12.
4. Attach the two rear idlers to the back rail using M5 screws and M5 square nuts (and washers). See a diagram of this on page 13 of the D-bot build guide pdf, although note that this part has been modified for the sand-table. Note that the screws are not shown in the renderings.
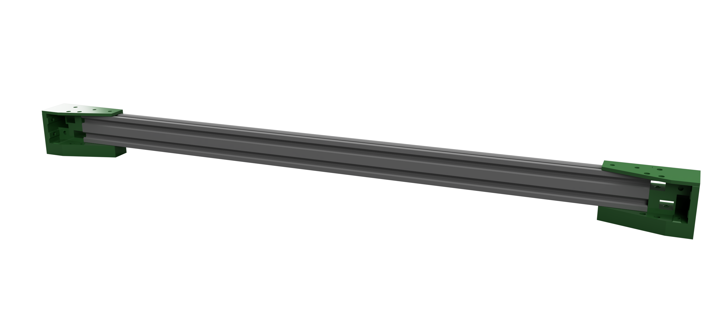
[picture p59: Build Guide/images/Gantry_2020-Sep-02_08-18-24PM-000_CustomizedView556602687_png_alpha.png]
   
5. Attach the side rails to the two rear idlers as shown:
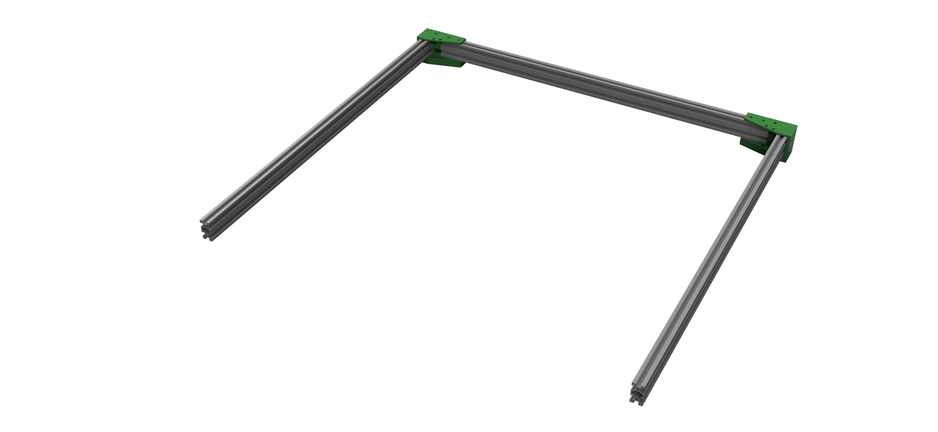
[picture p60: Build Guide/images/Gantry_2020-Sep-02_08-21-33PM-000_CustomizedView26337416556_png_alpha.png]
   
6. Attach the hbar idlers and print carriage to the hbar rail, and mount the hbar rail onto the current assembly. Pay close attention to the orientation of the idlers on the rail (whether the bearings are on the top/bottom, etc). Refer to the D-bot build guide pdf pages 39, 43-46 on how to do this. The belt clamps can also be mounted to the print carriage loosely at this step (see page 38 for how to do so). Note that the print carriage has been modified to hold a magnet instead of an 3d printer extruder. The magnet clamp (in red) can be attached using short M3 screws, washers and nuts (on the inside). A groove exists so that if the magnet is loose, a zip tie can be clamped around it to hold it in place (some electrical tape around the magnet helps increase the grip). I suggest that the magnet **should not** be installed until the very end, as it is quite powerful and could hurt someone.

- Note: the wheel spacers found in the STLs folder differ from the D-Bot buid guide - the spacers for this project have an added lip to minimize drag on the roller bearings. This has the effect of making the wheel spacers directional and they should be installed such that the lip is touching the bearing.

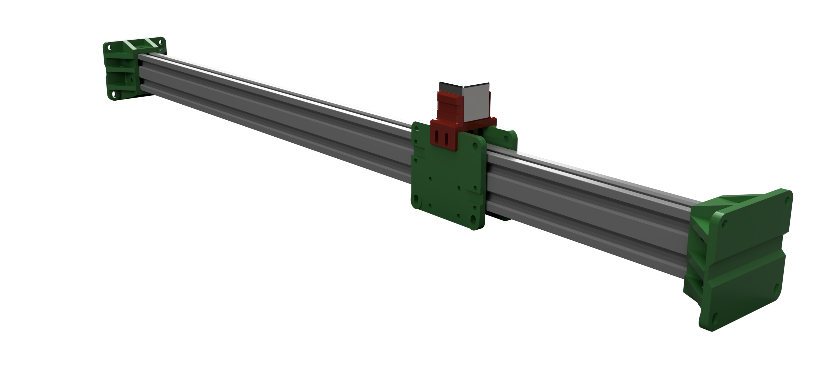
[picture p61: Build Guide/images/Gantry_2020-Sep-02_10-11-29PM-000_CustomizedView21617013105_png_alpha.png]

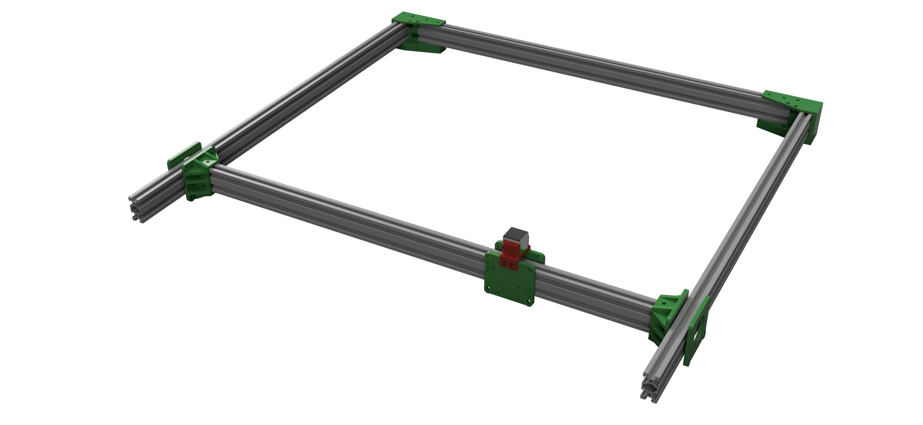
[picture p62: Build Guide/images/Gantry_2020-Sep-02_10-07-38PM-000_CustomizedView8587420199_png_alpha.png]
 7. You can now install the two motor mounts on the ends of the side rails. Make sure to install the stepper dampers if you bought those. The D-bot build guide pdf suggests driving M5 screws into the tapped holes of the v-slot extrusion; however, if you don't have a tap, this isn't necessary for the sand table.
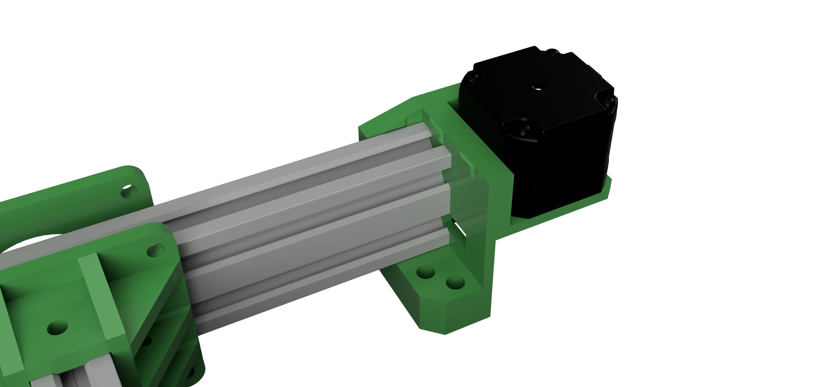
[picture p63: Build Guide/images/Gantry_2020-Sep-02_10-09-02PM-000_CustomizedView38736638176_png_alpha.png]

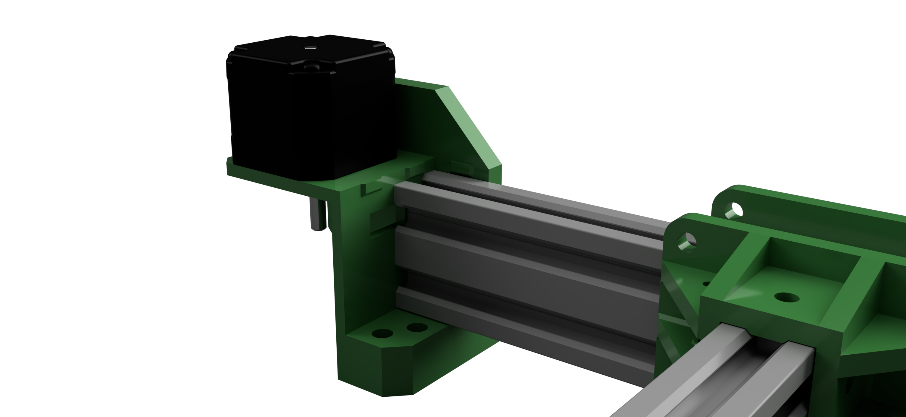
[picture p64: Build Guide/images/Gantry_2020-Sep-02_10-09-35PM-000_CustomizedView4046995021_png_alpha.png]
 8. Install the GT2 pulleys onto the motor shafts, aligned with the hole in the motor mount. Run the GT2 belt (the red and yellow paths are separate belts) through the assembly per the diagram below (found in the D-bot build guide pdf page 48). Then, tighten the belt clamps on the print carriage. They should be relatively tight, or the mechanism will not run well at speed.
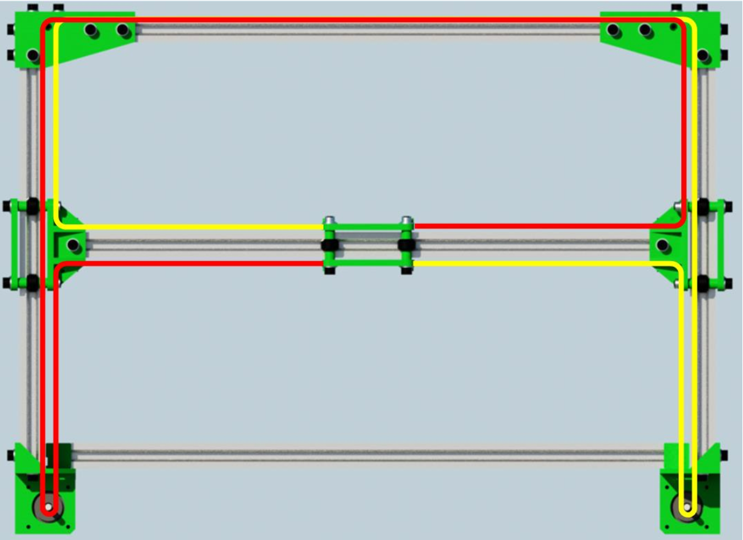
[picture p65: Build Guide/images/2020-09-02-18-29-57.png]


### Installing the gantry on the table

1. This is pretty simple. Take the time to align the gantry centered on the table though. **The margins on each side are unique**, so it's important to align the gantry taking into consideration the movement area of the print carriage, and not the physical size of the gantry.
2. Once aligned, use any type of screw and bolt down the four idlers to the table. I added a piece of foam underneath each of them to dampen the vibrations.

Here are a bunch of pictures that should hopefully clarify some things:












## Electronics/Software

While having electronics experience helps, it is not required to build this table. The electrical system is actually quite simple, and while it could be improved for robustness, it works well enough.

1. Install the RAMPS 1.6+ shield onto your Arduino MEGA. Take care to make sure that the pins line up when you push the two boards together.
2. Wire up your stepper drivers onto the RAMPS board for the X and Y motor slots. If you are using TMC2209's as per the BOM, make sure to wire up UART mode and sensorless homing functionality, which is explained quite well in https://youtu.be/dOJbSrWVu_Q?t=439 (follow instructions for the MKS Gen L and TMC 2209). Even though it's a different board, the AUX2 header referred in the video can also be found on the RAMPS board. The software should already be configured, so you can skip that step.
   
3. Install the LED Strip Arduino firmware onto the Arduino UNO, and the Marlin Arduino firmware onto the Arduino MEGA. On a fresh SD Card, install [Raspberry Pi OS with Debian Buster](https://downloads.raspberrypi.com/raspios_armhf/images/raspios_armhf-2021-05-28/2021-05-07-raspios-buster-armhf.zip), and configure for headless start (see https://www.raspberrypi.org/documentation/configuration/wireless/headless.md).
4. Wire up the rest of the components per the diagram in `sand_table_electronics_diagram.pdf`. Note that there is a 330 Ohm resistor connecting from the Arduino Uno to the LED Strip `DI` pin. This is extremely important, but any resistor from 220 to 470 ohms will work. If you don't have 330 Ohm resistors (and only the 1000 Ohm resistors from the BOM, you can wire three of those in parallel).
5. Use double-sided tape or some other adhesive to secure the components down on one side of the table (the same side as the hole you cut for the power wire).
6. Check and double check that all the connections are secure and correct, and then try powering the whole system on. If all is well, the Pi should boot (red light on, green light blinks a bunch), and nothing else should happen.

Here is an image of the result. Note the power wires running to each corner of the table: this is because I used four separate LED strips where I chained the data pins together...this is not necessary, and I did this only because that is what I had on hand.


### Raspberry Pi Setup/Webserver Installation

1. ssh into your Raspberry Pi. If you do not know how, this is something that is very easy to google. The default credentials should be `pi` as the username and `raspberry` as the password.
2. Change the default password to something else (See [this article](https://www.raspberrypi.org/documentation/linux/usage/users.md#:~:text=Once%20you're%20logged%20in,asked%20for%20a%20new%20password.) on how to do this)
3. Change your hostname if you desire (see [this article](https://www.tomshardware.com/how-to/raspberry-pi-change-hostname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) on how to do this...I changed my Raspberry Pi's hostname to `sandtable`)
4. Chances are that NodeJS should be installed, but it's version is outdated. To install the lastest version of NodeJS, type the following into the ssh terminal:

   ```bash
   curl -o- https://raw.githubusercontent.com/nvm-sh/nvm/v0.35.3/install.sh | bash
   export NVM_DIR="$HOME/.nvm"
   export NVM_DIR="$HOME/.nvm"
   [ -s "$NVM_DIR/nvm.sh" ] && \. "$NVM_DIR/nvm.sh"  # This loads nvm
   [ -s "$NVM_DIR/bash_completion" ] && \. "$NVM_DIR/bash_completion"  # This loads nvm bash_completion
   nvm install 14.18
   npm install -g npm@6.14
   ```

   If you get an error stating that the command `nvm` cannot be found, try closing your ssh connection and reconnecting.

   To confirm that NodeJS is on the latest version now, type `node -v` into the terminal.

5. Type the following into the ssh terminal:
   ```bash
   cd ~/Documents
   git clone https://github.com/rdudhagra/Sand-Table.git
   cd Sand-Table/Website
   npm install
   ```
6. Unfortunately, running on port 80 requires root privileges, but running the webserver using `sudo` is a bad idea. Therefore, we must set up an nginx server to act as a proxy.

   1. Type into a terminal:
      ```bash
      nano .env
      ```
      Edit the `PRODUCTION_PORT` variable to equal `3000`. Type `Ctrl`+`X`, then `Y` to save and exit. Also make sure that your Serial port variables are correctly set. To find the Serial port of your connected Arduinos, follow the following steps:
      1. Unplug all USB devices from the Pi
      2. Run `ls /dev/tty*`, note the output
      3. Plug in one of the usb devices, run the above command again. The additional entry is the serial port of this device.
      4. Plug in another device, run the above command again. The additional entry is the serial port of that device.
      5. Repeat for any additional devices.
   2. Follow the guide [here](https://eladnava.com/binding-nodejs-port-80-using-nginx/#nginx) to set up an nginx server. However, replace the contents of `/etc/nginx/sites-available/node` with:

      ```nginx
      server {
         client_max_body_size 50M;

         listen 80;
         server_name sandtable.local;

         location / {
            proxy_set_header   X-Forwarded-For $remote_addr;
            proxy_set_header   Host $http_host;
            proxy_pass         "http://127.0.0.1:3000";

            proxy_read_timeout 1800;
            proxy_connect_timeout 1800;
            proxy_send_timeout 1800;
            send_timeout 1800;
         }
      }
      ```

      This replacement config sets the port to 3000 and increases the max packet size limit, so that larger `.thr` (Sisyphus track format) files can be uploaded to the website.

7. With nginx set up now, we can try to run our website to make sure that everything works. Type into your terminal:
   ```bash
   cd ~/Documents/Sand-Table/Website
   npm run prod
   ```
   Wait a minute or two, then navigate to `http://[your Pi's ip address]` in a web browser. The website should pop up. If not, look for an error in the logs in your terminal, and make sure that nginx is actually running and properly configured. You should be able to turn on the lights at this point, and the gantry should move to the center of the table after homing.
8. With that confirmed, stop the webserver with `Ctrl+C`. We will now set up a systemd service, which will automatically run the webserver on startup.

   1. Create a new systemd file
      ```bash
      sudo nano /etc/systemd/system/sandtable.service
      ```
   2. Paste the following:

      ```bash
      [Unit]
      Description=Runs sand table webserver
      After=network.target

      [Service]
      ExecStart=/home/pi/Documents/Sand-Table/Website/start.sh
      WorkingDirectory=/home/pi/Documents/Sand-Table/Website
      StandardOutput=inherit
      StandardError=inherit
      Restart=always
      User=pi

      [Install]
      WantedBy=multi-user.target
      ```

   3. Start the systemd process like so:
      ```bash
      sudo systemctl start sandtable.service
      ```
   4. Confirm that it works by checking the status:
      ```bash
      sudo systemctl status sandtable.service
      ```
   5. If all is well, enable the service to start automatically on boot:
      ```bash
      sudo systemctl enable sandtable.service
      ```

That's it for the Raspberry Pi! If you see an error in any of these steps, don't hesitate to copy and paste the error into google...someone has most likely encountered the same situation as you, and a solution should be posted on some forum.

## Final Assembly

Now that the software works, we can finish the assembly of the sand table. After confirming that you can access the website from your computer/smartphone and that the gantry moves smoothly, **turn off** your sand table by unplugging the power supply.

1. Add the risers in the four corners of the table and glue them in place. I also zip-tied the magnet in place and added some rubber freezer mats to absorb some of the echo (no clue if this is effective or not).
   
2. Place the tray on top of the risers. You will then need to power on the table and move the magnet around and make sure that the magnet doesn't rub against the table. You want the magnet as close as possible to the sand tray without touching it. You can find tracks by searching for `sisyphus table tracks` on google.
3. Once leveled, attach something white to the top of the tray. I used canvas cloth, which works surprisingly well.
   
4. Next, it's time to install the led strips. Turn off the table. This will vary based on what LED strip you buy, but attach the strip around the edge of the tray, making sure that the input connector is on the correct corner of the table (the corner closest to the Arduino UNO). To pass the wires beneath the tray, I cut a groove just tall enough for the wires to wrap around and slide beneath the tray (there is a slight gap between the tray and the table walls).
   
5. With that done, turn on the table and test that the led strips work. Make sure that they are wired correctly before you turn anything on. If that works, add the two bags of sand and do your best to level it out. While the table can level the middle fine, the edges beyond the gantry's work area should be leveled by hand.
6. Add the ring on top, and then place the glass table top on top of the ring.

That's it...you're done! Your sand table should be fully operational and ready to play some tracks.


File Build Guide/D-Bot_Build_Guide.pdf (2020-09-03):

# D-Bot Core-XY 3D Printer

# Build and Configuration Guide

# March 2017

# D. Spaulding

## Disclaimer

This guide is meant to serve as an informational resource for building a D-Bot 3D printer. It is not meant to be a 100% complete instructional manual. This is not a commercial 3d printer kit, it is an experimental prototype design.

If you have no experience with power tools, mechanical assembly, electronics, or electrical wiring, please do not attempt this project. Incorrectly wiring electrical components, especially those involving AC line voltage can start fires or cause fatal injury.

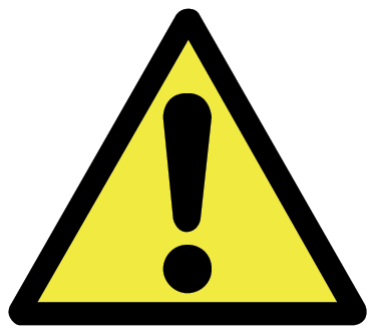
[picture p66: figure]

## Table of Contents

## 1. Introduction

- Format
This guide contains multiple hyperlinks for file downloads and reference videos. The recommended viewing method is via PC rather than printout.
- Background
The D-Bot printer is based on cfeniak’s C-Bot (http://www.openbuilds.com/builds/c-bot.1146/) printer, which was designed with the goal of making a robust scalable Core-XY 3D Printer. The D-Bot is just one example of a printer which uses that base design and builds upon it. The original C-bot design featured a cantilevered bed and the D-bot design attempts to have a more stable build platform by moving the Z motors forward so that the print bed is lifted from its center of gravity. The secondary goal of the D-Bot design was to reduce the overall cost of the printer without sacrificing build quality. Other differences include changing some rails to 20mm height instead of 40mm, relocation of the X and Y endstops to simplify homing, and modifications to printable parts either for structural or aesthetic reasons.
- Required Tools
1. Metric Tape Measure (http://amzn.to/2hKnLgs)
2. Metric Allen Wrenches (http://amzn.to/2hPjs0o)
3. Miter Saw or Hacksaw
4. M5 Thread Tap (http://amzn.to/2gQnIv9)
5. Phillips Screwdriver
6. Adjustable Crescent Wrench
7. Needle Nose Pliers
8. Digital Caliper (http://amzn.to/2hPpxu2)
9. Utility Knife
10. Wire Strippers
11. Wire Crimping Tool (http://amzn.to/2i4Tcia)
12. Soldering Iron w/ Solder
13. Multimeter
- Recommended Assembly Related Items
1. Heat Shrink Tubing (http://amzn.to/2h0EiM9)
2. Electrical Tape
3. Zip Ties
4. Super Glue
5. JB Weld Epoxy (http://amzn.to/2h0xUog)
6. Machine Oil

## 2. Ordering Parts

Read this build guide completely before ordering parts in case alternatives/ variants are wanted. Review the bill of materials, make sure you can buy all of the parts or find good alternatives and decide on optional components. Cheap ebay parts from china can take a month or more to arrive.

More information on parts selection:

- Hot End: This design uses an E3D V6 all metal hot end which can print PLA, ABS, and other filaments such as nylon. A cheaper option is the E3d lite6 which can print PLA and ABS for around half the cost.
- Control Board: This design uses a RAMPS/Arduino setup, which is one of the most common among DIY 3D printers, it is very cheap and simple and it works. Other options include Rumba/Rambo boards which are essentially RAMPS+Arduino on one board. Smoothieware based boards such as Smoothieboard or Azteeg X5 offer a different firmware option. Choose a control board which will give a good performance/cost ratio. This guide is written for a build using a Ramps 1.4 board.
- Heated Bed – The heated bed chosen for this design works well enough for PLA and PETG but it takes very long to reach ABS temps (100C) and it has trouble maintaining that temperature. For ABS printing, research different 200x300mm heated beds which are well reviewed for use in printing ABS.
- Other potential Extras:
- Auto bed leveling (aka crooked bed compensation) is not needed for this printer. This design features an X Y gantry which is very stable in the Z direction. Manual bed leveling only needs to be performed occasionally and it only takes a minute to achieve nearly perfect leveling with a playing card and an Allen wrench.
- LCD Display/SD storage can be implemented depending on the control board chosen. Many Ramps kits come with an LCD display. The default configuration for this printer is operating via a PC connection to Repetier Host for slicing, Gcode transmission, and print monitoring.

## 3. Cutting V-Slot Extrusions

- Layout, measure, and mark the six V-slot rails to the proper lengths as shown in Figure 1. Label alphabetically as shown, these labels will be referenced during assembly.
- Cut V-slot railing pieces before printing plastic parts. If there are incorrect cuts made, plastic parts adjacent to the affected rail(s) can be modified to compensate for slightly incorrect cuts (this may or may not have happened to the author of this guide).
- Alternate frame railing lengths sized for a 300x300mm bed are shown in the appendix.
- Options for cutting:
1. Cut with a hacksaw – ok quality, if done carefully
2. Miter saw with a wood blade – somewhat ok, if done correctly
3. Miter saw with non-ferrous blade (http://amzn.to/2hXIspN) – best, this approach can give perfect clean cuts
4. If you do not have access to the proper tools, contact a local metal shop, mechanic, welder, or other professional that can cut aluminum railing to length for a (hopefully small) fee.
- Do not use an abrasive blade chop saw (http://pop.h-cdn.co/assets/cm/15/05/54c7e09f406a3_-_chop-saw-08-0115-lgn.jpg) meant for cutting steel. It will leave very jagged rough cuts because it melts aluminum when cutting through.
- Measure twice, cut once!
- 20x40mm V-slot Railing pieces needed:
(4) at 520mm - A, B, C, D
(1) at 463mm - G
(1) at 488mm - R
(1) at 448mm - Q
(2) at 333mm - E, F
(2) at 313mm - O, P
- 20x20mm V-slot Railing pieces needed:
(3) at 463mm - L, M, N
(1) at 503mm - K
(2) at 313mm - H, J

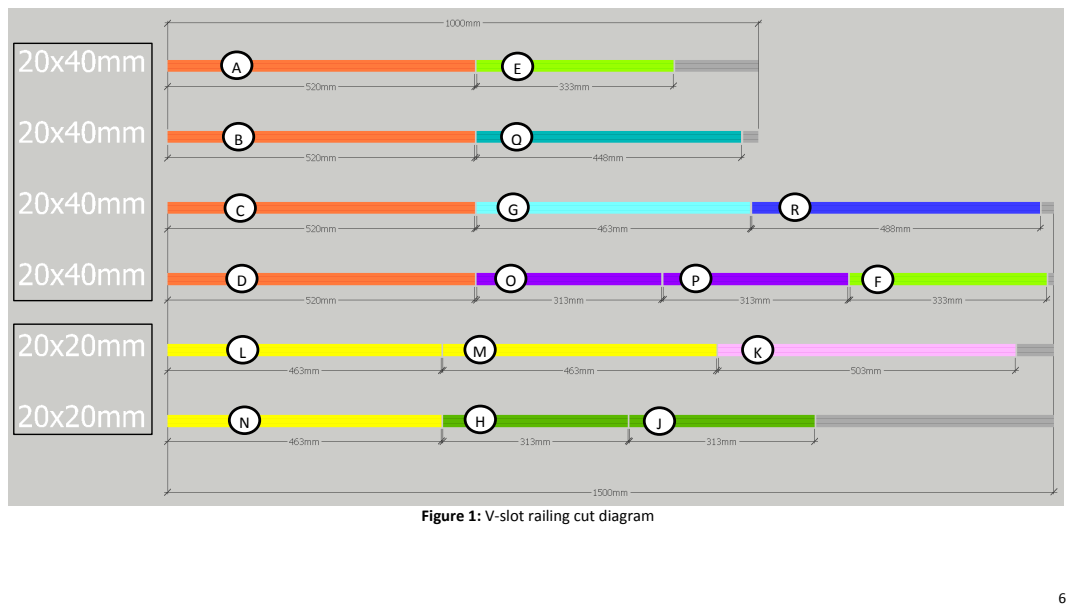
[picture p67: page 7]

Figure 1: V-slot railing cut diagram

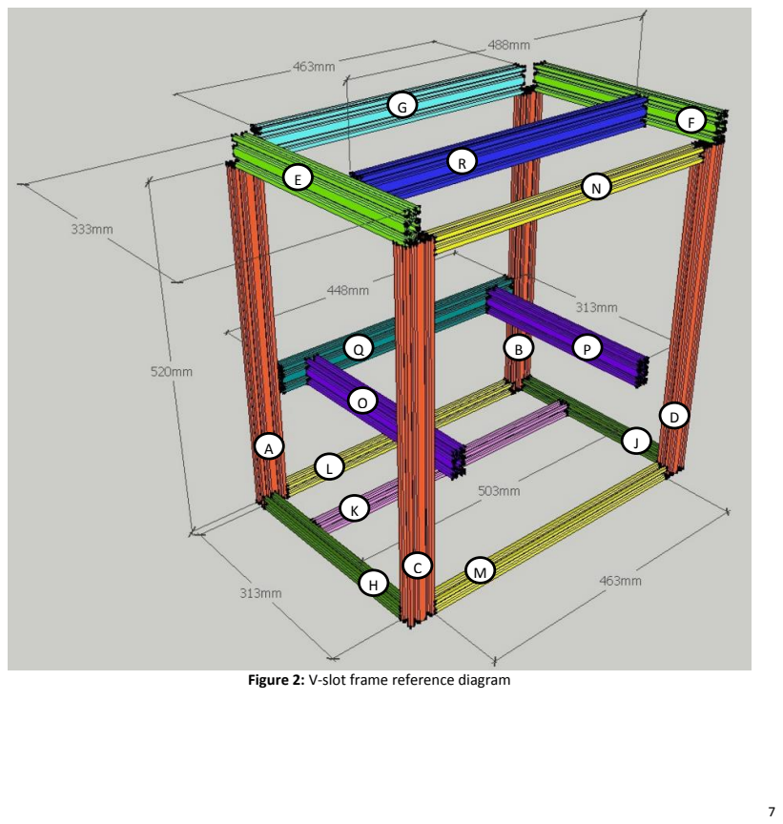
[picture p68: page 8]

Figure 2: V-slot frame reference diagram

- Figure 3 shows which locations on the V-slot rails need to be M5 thread tapped. V-slot ends are predrilled correctly to the size needed for M5 threads. Use oil on the thread tap, repeatedly reverse the tap to avoid jamming and breaking. Practice thread tapping on some of the leftover scrap V-slot pieces. Here is an example thread tapping video. (https://youtu.be/U5QU_3qUigk)

Figure 3: M5 Thread Tap Locations

A

B | C

D

E

F

## 4. Printing Parts

- All printable parts required are on the D-Bot Thing Files Page. (http://www.thingiverse.com/thing:1001065/#files) The required quantity for each part type is indicated by the number at the beginning of each file name.
- Parts with stacked countersink holes will print with a single solid layer in between the openings. This is to allow smaller cylinders to print on top of larger cylinders without print failure. Filler material layers can be removed with a knife or screwdriver.
- Optional components can be printed on the D-Bot itself and added later to avoid extra initial printing. This is especially helpful when parts must be printed on a shared public printer or bought from a third party.
- Any part which will be bolted to the aluminum frame has the potential to crack when tightened. This can be avoided by printing structural parts at 100% infill or at least a high infill percentage and several shells which will provide more structure behind mounting holes. It will take more plastic but it is worth it to have all parts as rigid as possible for a strong frame.
- If possible, print structural parts in PETG or ABS rather than PLA. After a few months of use, printers with PLA components exhibit cracked edges due to vibration even when printed at 100% infill.

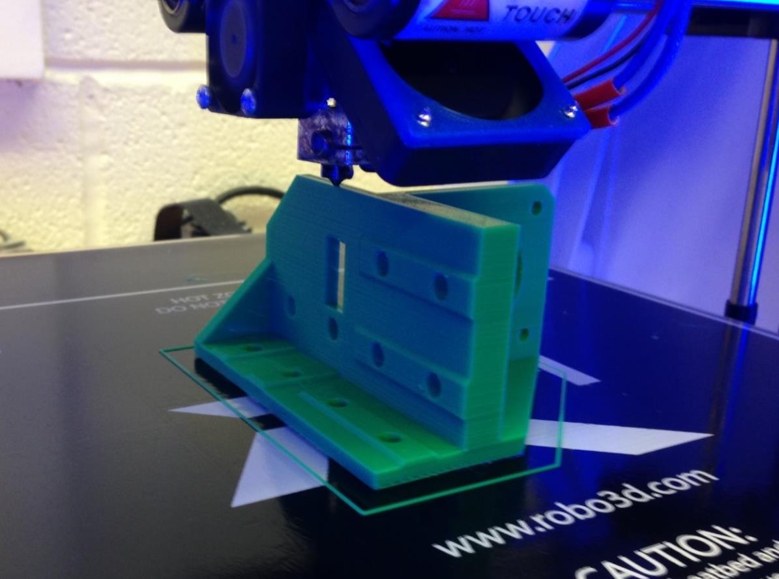
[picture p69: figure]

Figure 4: Printing the Right Front Motor Mount

## 5. Mechanical pre-assembly

- Assemble Wheel Units (20 total)
Each wheel unit consists of an openbuilds mini V wheel with a MR105ZZ bearing inserted on each side and a 1mm shim in between the two bearings. Do not forget the 1mm shims, without them the spacers will push in on the bearings and they will bind when tightened, the shim gives something for the bearings to push against so they will not bind. Assemble all 20 wheel units per Figure 5.

Parts Needed:
(20) OpenBuilds mini V wheels
(20) Printed Bearing Shims (Or Openbuilds mini Vwheel precision shims)
(40) MR105ZZ Bearings

Figure 5: Wheel unit Assembly

- Rear Idler bearings
Insert idler bearing assemblies into the rear left and right idlers (4 locations) as shown in Figure 6. The idler bearing assembly is: (bolt > plastic > flange bearing > washer > flange bearing > plastic > nut), mounted in each rear idler housing. One bolt is inserted from above and one is inserted from below. The lower idler bolt is inaccessible after frame assembly.

Parts Needed:
(8) F623ZZ Flanged Bearings
(4) M3 25mm bolts
(4) M3 Nuts (standard)
(4) M3 washers

Figure 6: Rear Idler Bearing Assembly

- H-Bar End Idler bearings
Insert idler bearing assemblies into the left and right H Bar Ends (4 locations) as shown in Figure 7. The H-Bar idler bearing assembly is: (bolt > washer > plastic > flange bearing > washer > flange bearing > plastic > washer > nylock nut), mounted in each H Bar end. One bolt is inserted from above and one is inserted from below.

Parts Needed:
(8) F623ZZ Flanged Bearings
(4) M3 25mm bolts
(4) M3 Nuts (nylock)
(12) M3 washers

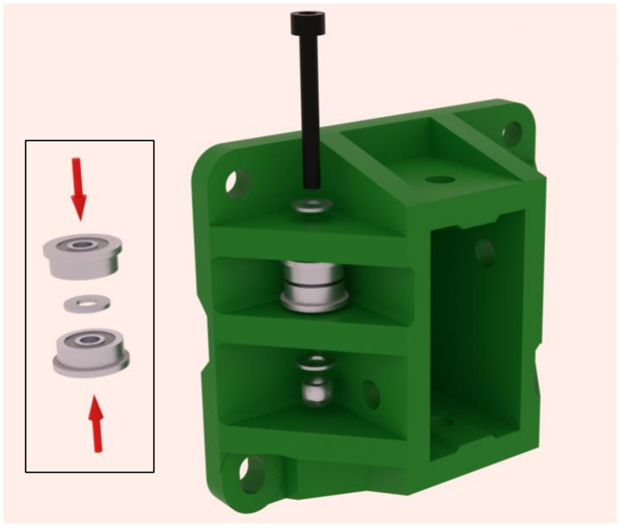
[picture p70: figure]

Figure 7: H-Bar End Idler Bearing Assembly

## 6. Frame Assembly

- Put an M5 10mm bolt with an M5 washer through each plastic frame part where needed and put a square nut on the end of the bolt. Leave off the 14 bolts which attach to tapped holes for now. Some M5 bolt mounting locations are countersunk and do not need M5 washers. Once nuts and bolts are placed on plastic pieces, slide each part onto the V-slot rail from the open end as shown in Figure 8. The square nuts need to be lined up with the V-slot ends.

Figure 8: V-Slot and square nut alignment

- For future add-ons or changes, square nuts can be inserted into the face of the V-slot rails after the frame has been assembled. Insert the square nut into the slot at an angle and tilt up, a small tap pushes it past the lip of the railing.

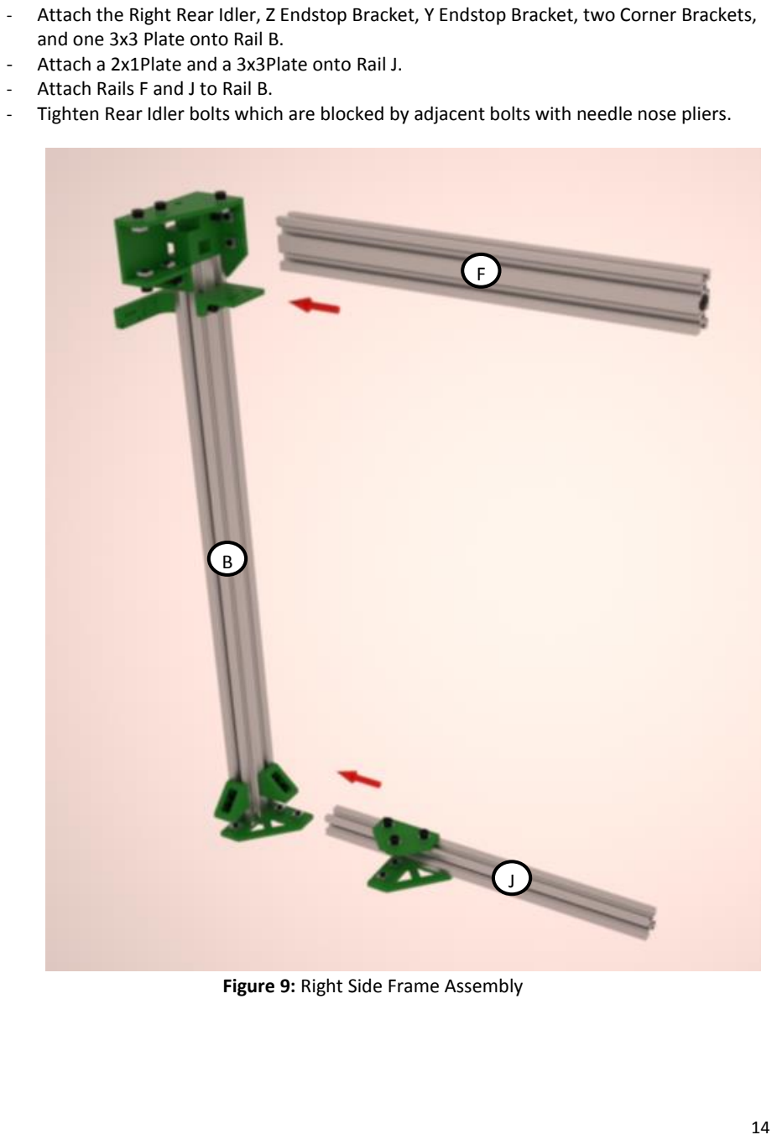
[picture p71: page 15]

- Attach the Right Rear Idler, Z Endstop Bracket, Y Endstop Bracket, two Corner Brackets, and one 3x3 Plate onto Rail B.
- Attach a 2x1Plate and a 3x3Plate onto Rail J.
- Attach Rails F and J to Rail B.
- Tighten Rear Idler bolts which are blocked by adjacent bolts with needle nose pliers.

Figure 9: Right Side Frame Assembly

B

J

F

- Attach the Right Motor Mount, two Corner Brackets, and one 3x3Plate to Rail D.
- Attach Rail D to complete the right side of the frame.

Figure 10: Right side Frame Assembly Continued

D

B

J

F

- Attach the Left Rear Idler, two Corner Brackets, and one 3x3Plate onto Rail A.
- Attach a 2x1Plate and a 3x3Plate onto Rail H.
- Attach Rails E and H to Rail A.

Figure 11: Left Side Frame Assembly

A

E

H

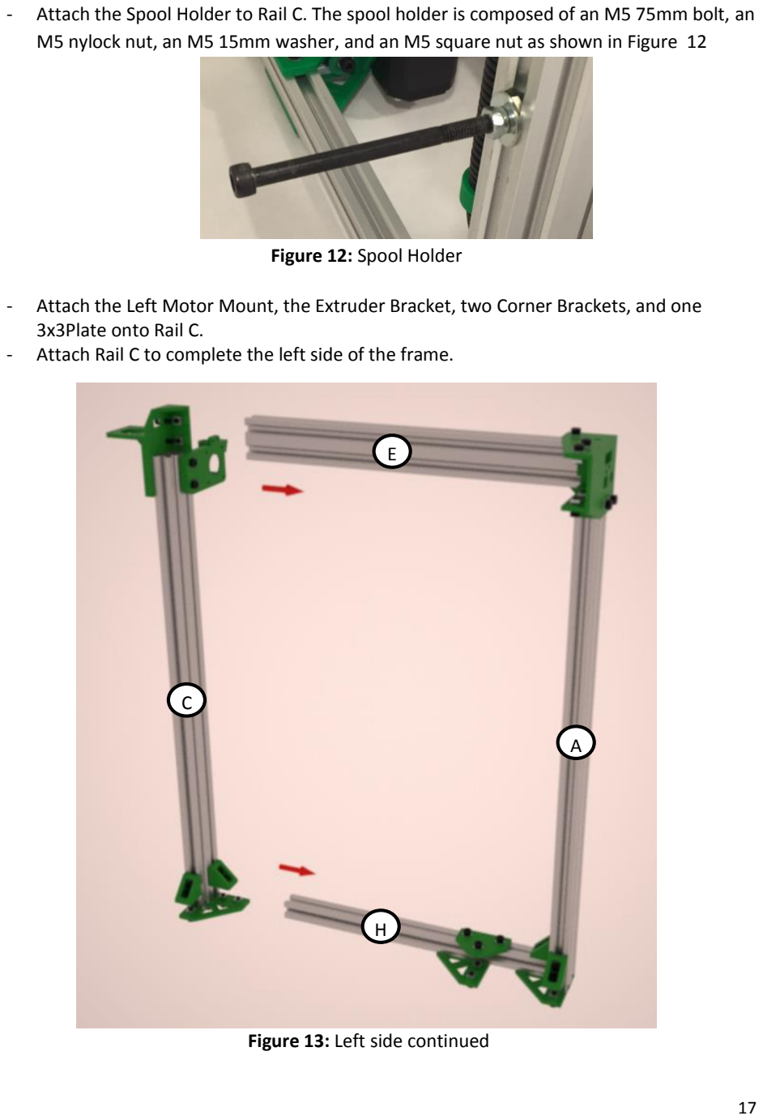
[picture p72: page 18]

- Attach the Spool Holder to Rail C. The spool holder is composed of an M5 75mm bolt, an M5 nylock nut, an M5 15mm washer, and an M5 square nut as shown in Figure 12

Figure 12: Spool Holder

- Attach the Left Motor Mount, the Extruder Bracket, two Corner Brackets, and one 3x3Plate onto Rail C.
- Attach Rail C to complete the left side of the frame.

Figure 13: Left side continued

A

E

H

C

- Attach two Z Motor Mounts to Rail K.
- Attach Rails G, L, K, and M to the right side frame assembly.

Figure 14: Middle Rail Assembly

L

M

G

K

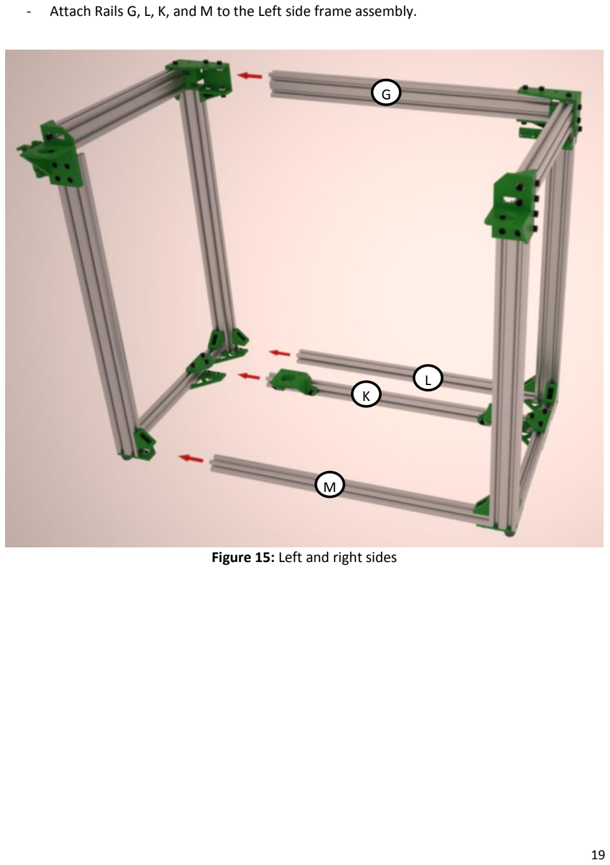
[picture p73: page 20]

- Attach Rails G, L, K, and M to the Left side frame assembly.

Figure 15: Left and right sides

L

M

G

K

- Attach two Corner Brackets onto Rail N.
- Attach Rail N to the front of the frame assembly

Figure 16: Center front rail

24mm | 24mm

- Adjust the following parts according to the dimensions shown. Tighten bolts.

31.5mm

69mm

- Attach four rubber feet to the four corners of the bottom with M5 10mm bolts.
- Attach remaining bolts which thread into tapped ends indicated in Figure 3 (14 total).
- Tighten all M5 frame bolts snugly but not tight enough to cause cracking of plastic parts.
- Measure between Rails A and B at the top and bottom of the frame, verify that the two rails are parallel to within 0.5mm. Loosen up lower corner brackets or rear idlers to make adjustments and leave a slight gap at the end of either Rail L or G in order to make rails A and B parallel.
- Measure between Rails E and F using the same technique, make adjustments to the gaps at the end of Rails G or N so that Rails E and F are parallel to within 0.5mm.

Figure 17: Assembled Frame

## 7. Z Platform Assembly

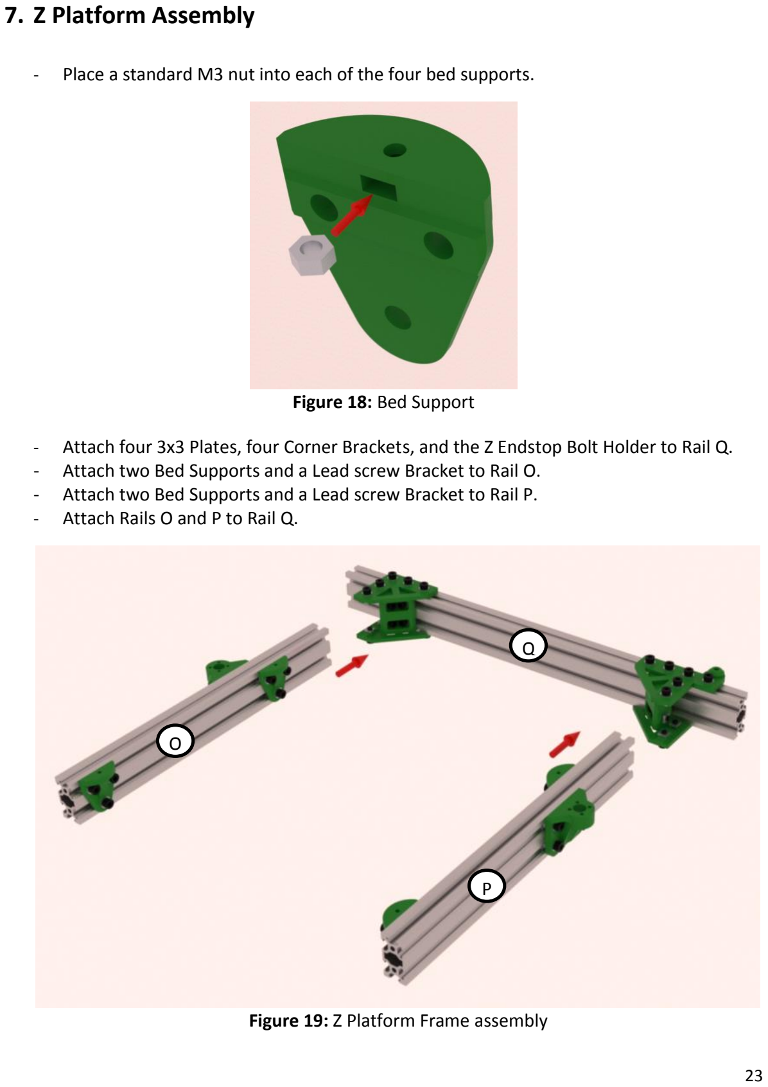
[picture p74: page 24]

- Place a standard M3 nut into each of the four bed supports.

Figure 18: Bed Support

- Attach four 3x3 Plates, four Corner Brackets, and the Z Endstop Bolt Holder to Rail Q.
- Attach two Bed Supports and a Lead screw Bracket to Rail O.
- Attach two Bed Supports and a Lead screw Bracket to Rail P.
- Attach Rails O and P to Rail Q.

Figure 19: Z Platform Frame assembly

Q

O

P

- Adjust Z platform parts according to Figure 20. Both sides are symmetrical.
- Verify that the distance between rail O and rail P is 317mm.

Figure 20: Z Platform Dimensions

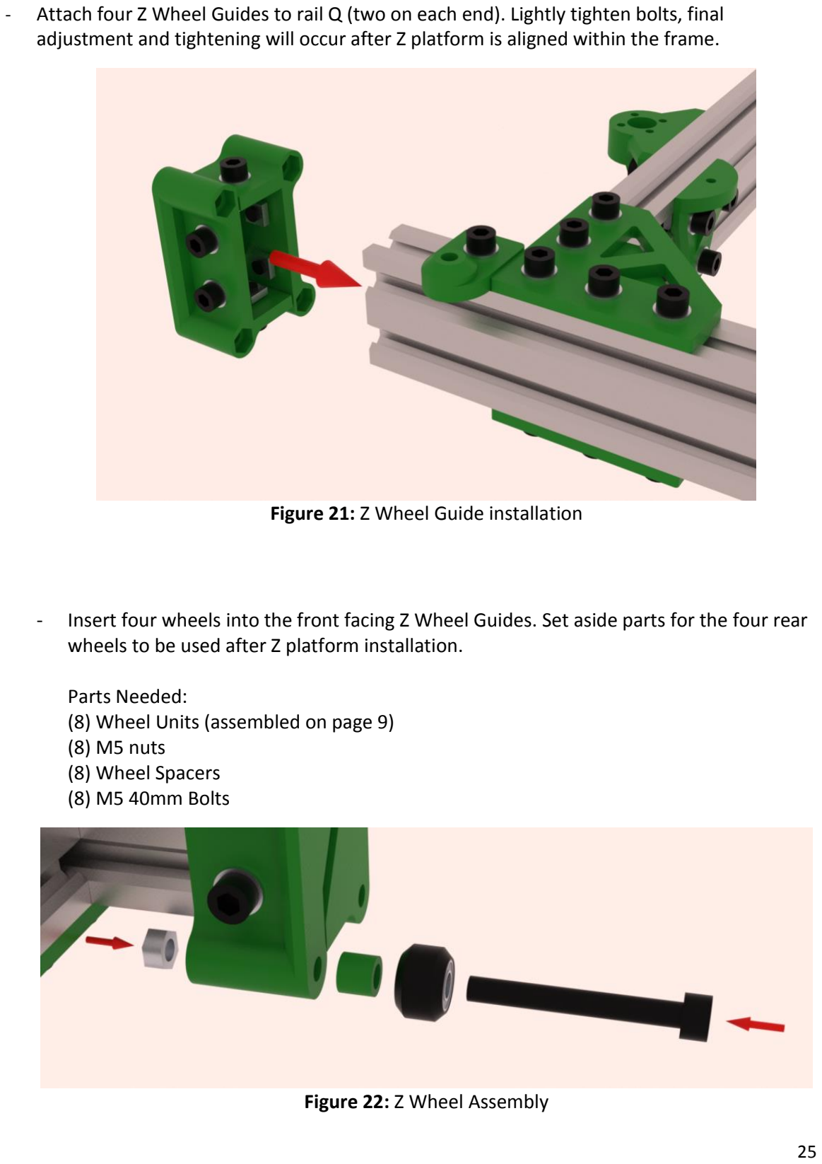
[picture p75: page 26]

- Attach four Z Wheel Guides to rail Q (two on each end). Lightly tighten bolts, final adjustment and tightening will occur after Z platform is aligned within the frame.

Figure 21: Z Wheel Guide installation

- Insert four wheels into the front facing Z Wheel Guides. Set aside parts for the four rear wheels to be used after Z platform installation.

Parts Needed:
(8) Wheel Units (assembled on page 9)
(8) M5 nuts
(8) Wheel Spacers
(8) M5 40mm Bolts

Figure 22: Z Wheel Assembly

- Install the Z platform into the frame, rest platform on the Z motor mounts.
- Line up the four Z wheels with the rear legs. Loosen the Z Wheel Guide bolts and adjust as needed to align the Z wheels with the V-slot grooves in the legs.

Figure 23: Z Platform installation into frame

- Insert four wheels into the rear Z Wheel Guides.

Figure 24: Rear Z Wheel installation

- Tilt the frame forward.
- Roll the Z platform from the top of the frame to the bottom and back.
- Adjust Z wheels and Z guide M5x10 bolts as needed for smooth motion.
- Wheels should be snug against the V-slot grooves but not too tight as to resist motion.
- The pairs of M5x10 Z guide bolts control the tightness of the wheels against rails.
- All 8 wheels should have equal pressure against the legs when rotated by finger.
- These steps may require multiple fine tunings to get all wheels aligned and evenly tight.

Figure 25: Z Platform Movement Testing

- Insert two brass lead screw nuts into the lead screw brackets and bolt in place as shown in Figure 26.

Parts Needed:
(2) Brass lead screw nuts
(8) M3 20mm Bolts
(8) M3 Nylock nuts

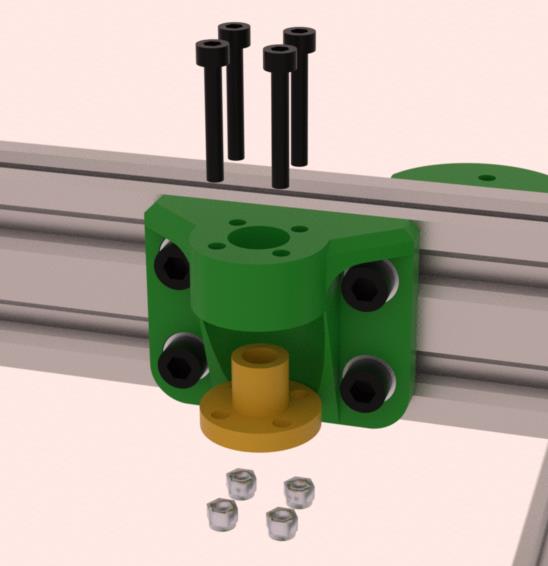
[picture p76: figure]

Figure 26: Leadscrew Nut Installation

- Connect the two lead screws to two motors using 5mm x 8mm flex couplings.
- The end of the lead screw should be seated against the top of the motor shaft.
- If there is space between the lead screw and motors shaft, the bed will not be stable.
- Thread the lead screws into the brass lead screw nuts as shown.

Figure 27: Z Motor and lead screw installation

- Bolt the Z motors to the Z motor brackets with M3 8mm bolts.

Parts Needed:
(8) M3 8mm bolts
(8) M3 Washers

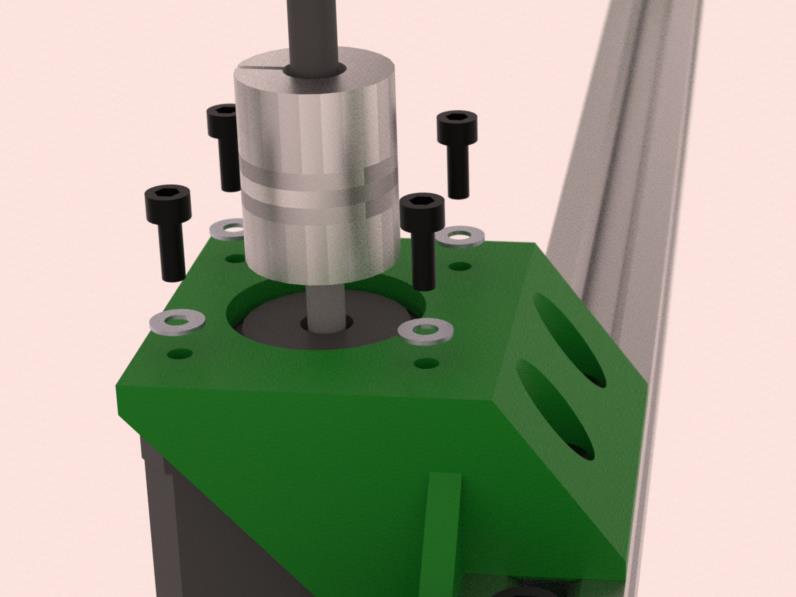
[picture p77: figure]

Figure 28: Z Motor bolts installation

- Move the Z platform all the way to the bottom of the frame.
- The brass lead screw nuts need to be centered over the Z motors as shown in Figure 29.
- Adjust the lead screw brackets in the Y direction as needed.
- Adjust the motor mounts in the X direction as needed.
- When aligned properly, the bed should move from the top of the frame to the bottom without binding, and the lead screws should be vertically straight when the bed is at the bottom of the frame as shown in Figure 30.

Figure 29: Lead Screw centering alignment

Figure 30: Lead Screw alignment

- Install the heated bed PCB as shown in Figure 31.
- The bed will be removed later to attach wiring.
- Attach the corkboard insulator to the bottom of the heated bed using JBweld epoxy.
- Place the bed thermistor in the hole in the center of the heated bed so that it touches the glass, secure the thermistor in place with thermally conductive epoxy.
- The distance between the bottom of the bed and the top of the bed bracket is ~8mm.

Parts Needed:
(4) M3 20mm bolts
(8) M3 Washers
(4) Bed Leveling Springs, similar to the dimensions below: ~4.7mm outside diameter
~12.6mm uncompressed length
~6.10mm fully compressed length

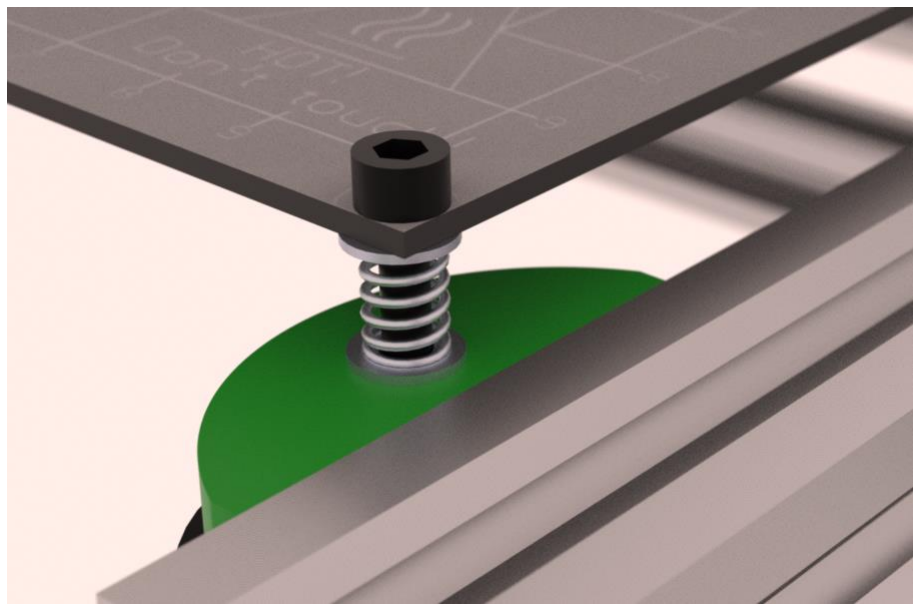
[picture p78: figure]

Figure 31: Heated Bed PCB Installation

- Attach glass plate to the bed with small binder clips.
- Standard ~3mm thick window glass works well.
- Match glass dimensions to the dimensions of the bed and have the glass corners notched to avoid hitting the bed mounting bolts. If notching glass corners is not an option, use a rectangular glass plate which will fit in between the mounting bolt heads.

## 8. Print Carriage Assembly

- Insert 10 M3 standard nuts into the openings of the front print carriage plate.
- Insert 8 M3 standard nuts into the openings of the rear print carriage plate.
- A small amount of adhesive on the outer edge of each nut helps them stay in place during assembly.

Figure 32: Front and Rear Print Carriage M3 nuts

- Assemble the E3D V6 Hot End according to this guide. (http://wiki.e3d-online.com/wiki/E3D-v6_Assembly)
- Attach the hot end to the front carriage plate as shown in Figure 33.

Parts Needed:
(2) M3 8mm bolts
(2) M3 25 mm bolts
(2) Printed hot end clamp pieces

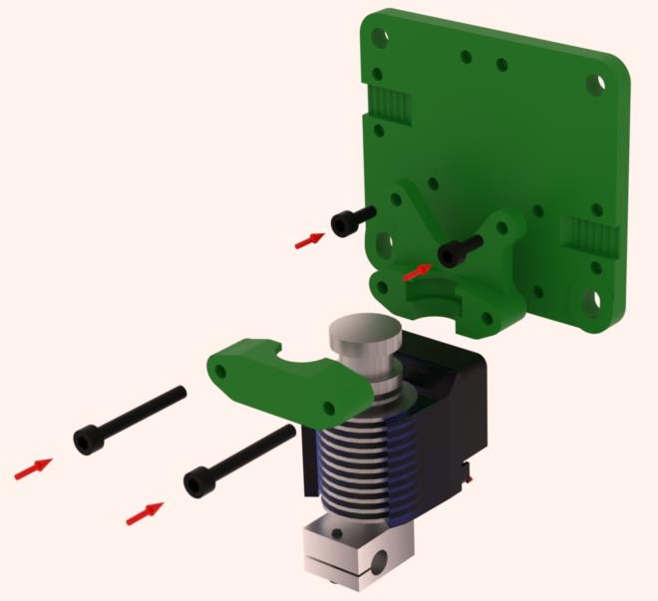
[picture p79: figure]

Figure 33: Hot end installation

- Install the tubing holder with two M3x8mm bolts as shown in Figure 34.

Figure 34: Tubing holder installation

- Attach the X Endstop to the rear print carriage plate using two M3x8mm bolts and 6 M3 washers to avoid having the bolts hit the V-slot rail behind the carriage.

Figure 35: X Endstop Installation

- Attach the 40mm fan to the duct as shown in Figure 36.
- Airflow direction arrow on fan should point towards duct.

Parts Needed:
(4) M3 20mm bolts
(4) M3 Nylock Nuts
(8) M3 Washers

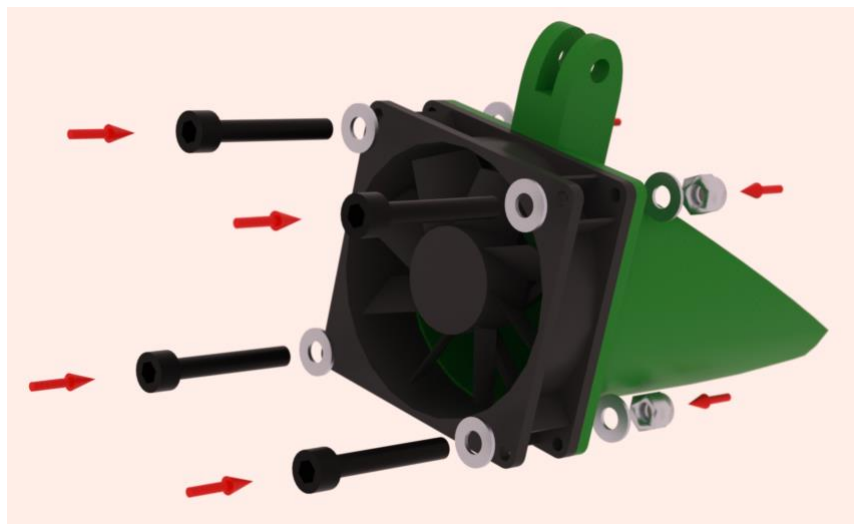
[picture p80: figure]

Figure 36: Part Cooling Fan Assembly

- Attach the fan duct to the fan swivel bracket as shown in Figure 37.

Parts Needed:
(1) M3 20mm bolt
(1) M3 Nylock Nut
(2) M3 Washers

Figure 37: Part Cooling Fan and Swivel Bracket Assembly

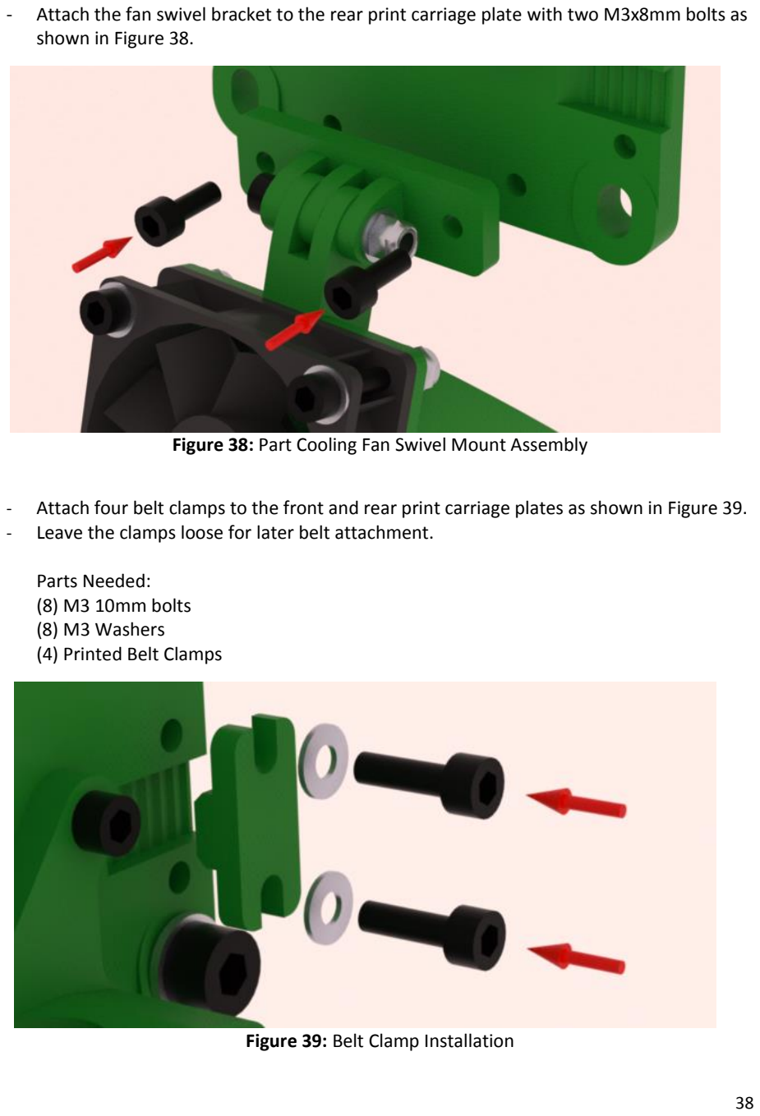
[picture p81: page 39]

- Attach the fan swivel bracket to the rear print carriage plate with two M3x8mm bolts as shown in Figure 38.

Figure 38: Part Cooling Fan Swivel Mount Assembly

- Attach four belt clamps to the front and rear print carriage plates as shown in Figure 39.
- Leave the clamps loose for later belt attachment.

Parts Needed:
(8) M3 10mm bolts
(8) M3 Washers
(4) Printed Belt Clamps

Figure 39: Belt Clamp Installation

- Bolt the front and rear print carriage plates together as shown in Figure 40.
- Verify that there are no M3 bolts extending beyond the backside of each plate.
- The final print carriage assembly is shown in Figure 41.

Parts Needed:
(4) M5 40mm bolts
(8) M5 Washers
(4) M5 Nylock nuts
(8) Printed Wheel Spacers (7mm tall)
(4) Wheel Units (assembled on page 9)

Figure 40: Print Carriage wheel assembly exploded view

Figure 41: Completed Print Carriage Assembly

## 9. XY Gantry Assembly

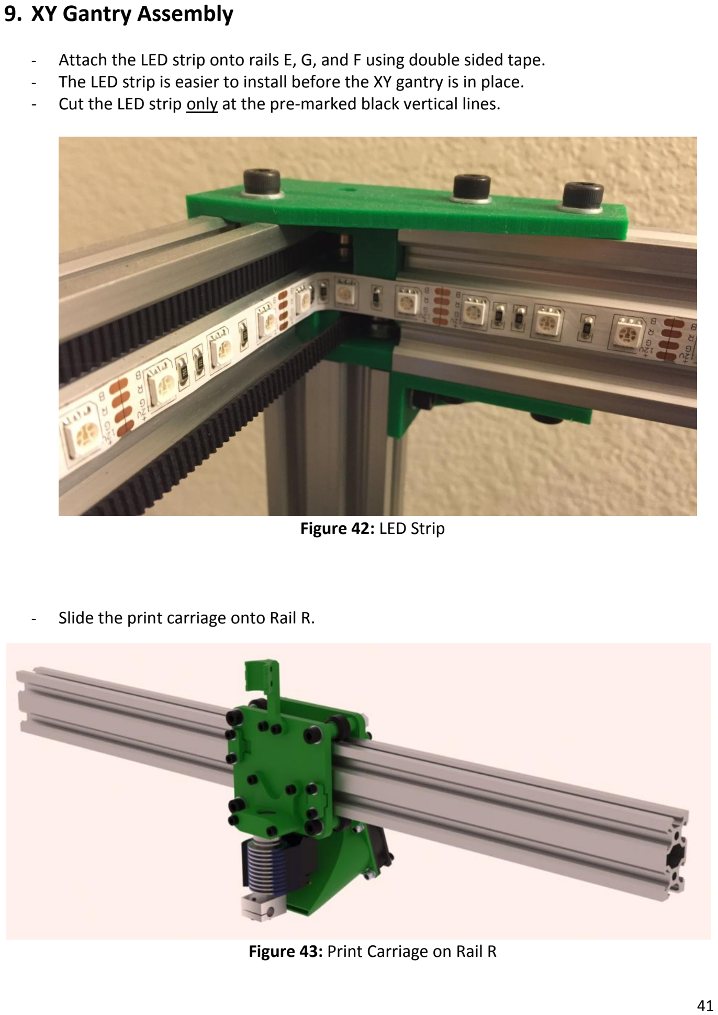
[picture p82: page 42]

- Attach the LED strip onto rails E, G, and F using double sided tape.
- The LED strip is easier to install before the XY gantry is in place.
- Cut the LED strip only at the pre-marked black vertical lines.

Figure 42: LED Strip

- Slide the print carriage onto Rail R.

Figure 43: Print Carriage on Rail R

- Attach the X Endstop Flange on the backside of Rail R as shown in Figure 44.
- The Endstop flange should be 37mm from the end of the rail

Parts Needed:
(1) M5 10mm bolt
(1) M5 Square Nut
(1) M5 Washer
(1) M3 25mm bolt

Figure 44: X Endstop Flange placement

- Insert an M5 20mm bolt in the bottom side of the Right H-Bar End as shown.
- This bolt will make contact with the Y Endstop switch.

Figure 45: Y Endstop Bolt placement

- Attach the right H-bar end piece to the right end of rail R as shown in Figure 46.
- Attach the left H-bar end piece to the left end of Rail R.
- Tapered mounting holes should be at the bottom of the H-bar ends.
- Loosely tighten bolts, final tightening will happen later.

Parts Needed:
(8) M5 10mm bolt
(8) M5 Square Nut
(8) M5 Washer

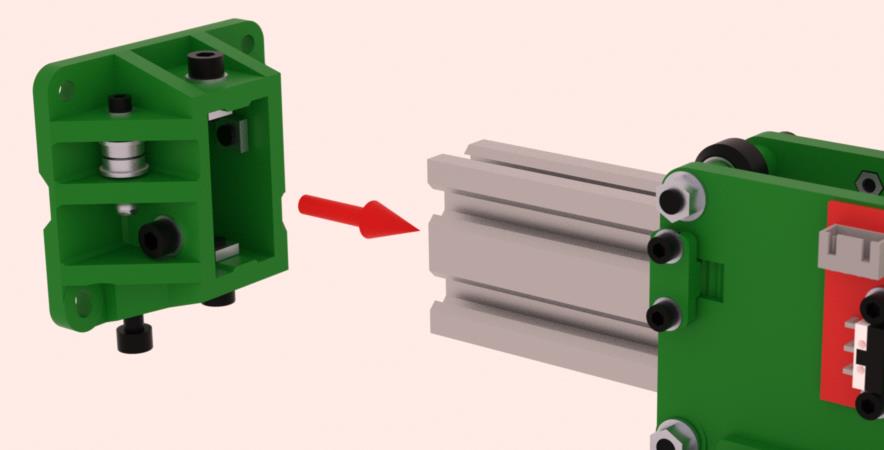
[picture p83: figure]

Figure 46: Right side H-bar end installation

- Attach an H-bar end plate and wheels to the right H-bar end as shown in Figure 47.
- Attach an H-bar end plate and wheels to the left H-bar end.
- Tapered mounting holes should be at the bottom of the H-bar endplate and point out.
- Leave the four lower wheels off until after the XY gantry is installed in the frame.

Parts Needed:
(4) M5 40mm bolts
(8) M5 Washers
(4) M5 Nylock nuts
(8) Printed Wheel Spacers (7mm tall)
(4) Wheel Units (assembled on page 9)

Figure 47: Right side H-bar endplate installation

Figure 48: Assembled XY Gantry before frame installation

- Loosen the 8 M5 bolts which hold the H-bar ends to rail R.
- Install the XY gantry into the frame as shown in Figure 49.
- Adjust the H-bar ends until the wheels are centered on the V-slot grooves.

Figure 49: XY Gantry installation into frame

- Install the four lower wheels on the left and right H-bar ends as shown in Figure 50.
- The tapered slopes around the lower wheel mount holes allow the wheels to be tightened against the V-slot by tightening the M5 40mm bolts.

Parts Needed:
(4) M5 40mm bolts
(8) M5 Washers
(4) M5 Nylock nuts
(8) Printed Wheel Spacers (7mm tall)
(4) Wheel Units (assembled on page 9)

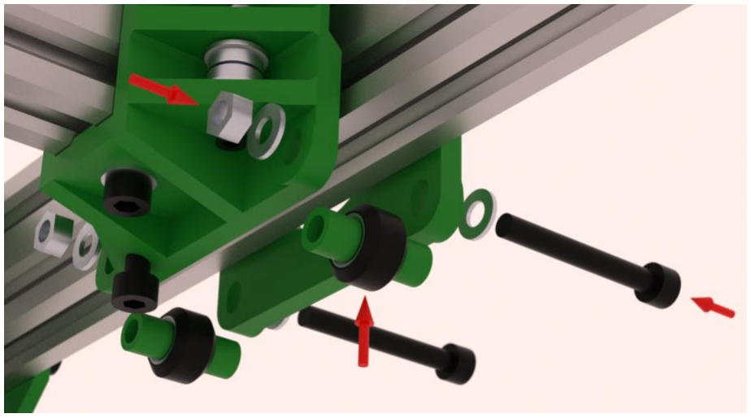
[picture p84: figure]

Figure 50: Lower XY gantry wheels installation

- Adjust all 12 XY gantry wheels until each wheel has equal tension against the V-slot rails.
- Slide the print carriage and the XY gantry back and forth to verify proper motion.
- Tighten the eight M5 10mm bolts which hold the H-bar ends to rail R.
- Install the two Core-XY motors on the front of the frame as shown in Figure 51.
- Install a 16 tooth GT2 pulley on each of the two Core-XY motors.

Parts Needed:
(8) M3 8mm Bolts
(8) M3 Washers

Figure 51: Core-XY Motor Installation

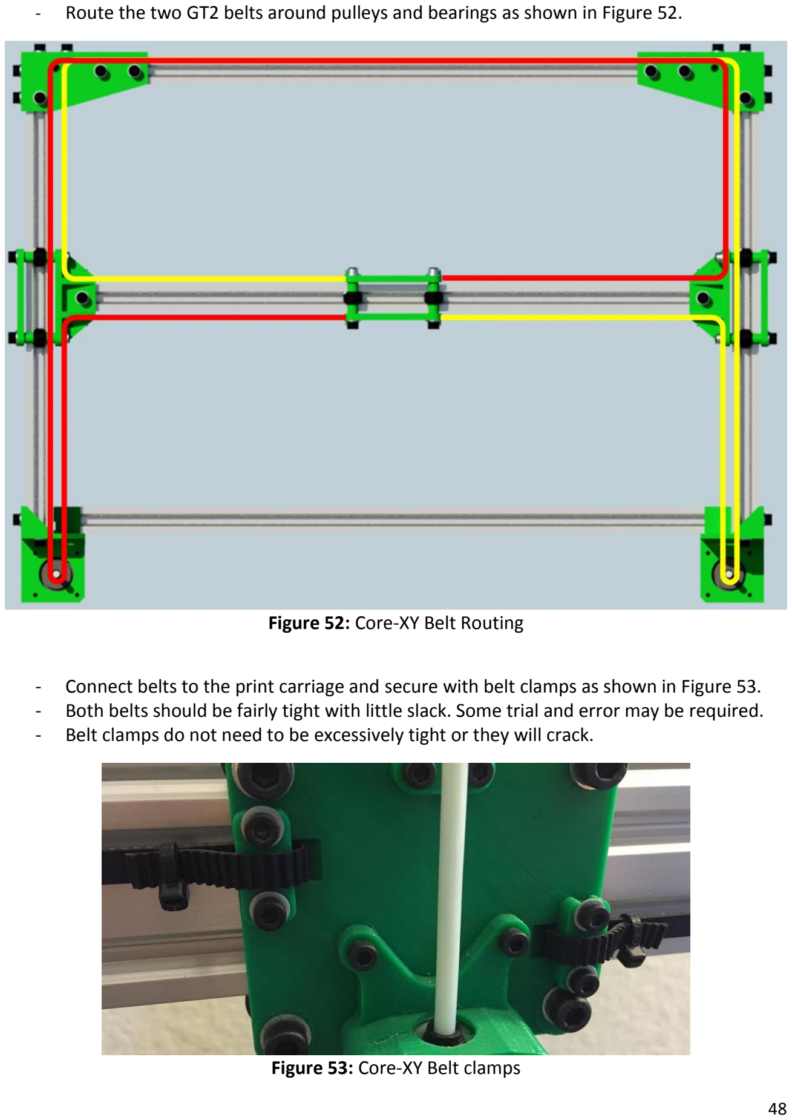
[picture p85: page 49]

- Route the two GT2 belts around pulleys and bearings as shown in Figure 52.

Figure 52: Core-XY Belt Routing

- Connect belts to the print carriage and secure with belt clamps as shown in Figure 53.
- Both belts should be fairly tight with little slack. Some trial and error may be required.
- Belt clamps do not need to be excessively tight or they will crack.

Figure 53: Core-XY Belt clamps

## 10. Extruder Assembly

- Install the extruder stepper motor with three M3x8mm bolts as shown in Figure 54.
- Attach the MK8 extruder gear to the motor, align teeth with filament holes.

Figure 54: Extruder motor

- Install the extruder tubing holder with two M3x8mm bolts as shown in Figure 55.

Figure 55: Extruder tubing holder

- Assemble the extrusion tensioner flange as shown in Figure 56.

Parts Needed:
(1) 625ZZ Bearing
(1) M5 12mm Bolt
(1) M5 Nylock Nut

Figure 56: Extruder tensioner flange assembly

- Attach the tensioner flange to the extruder with an M3x10mm bolt as shown.

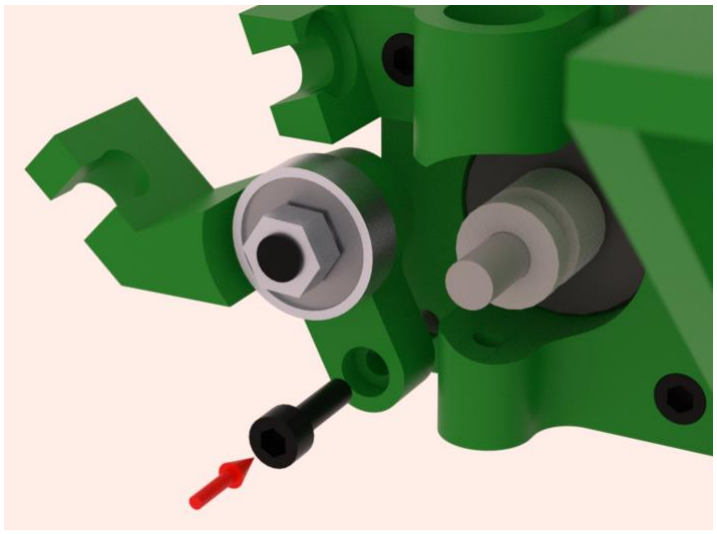
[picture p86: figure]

Figure 57: Extruder tensioner flange Installation

- Install the black bowden tube connector fitting into the top of the extruder as shown.
- The printed opening for the bowden tube connector may need to be widened with a file or knife blade to allow a good fit of the connector threads since the printed part is prone to cracking if the opening is too small. If the connector is too loose in the opening, super glue can be applied to the threads before inserting the bowden connector.
- Insert the bowden tube into the black bowden tube connector, leave the other end disconnected until later.
- Install the extruder tensioner spring as shown in Figure 58.

Parts Needed:
(1) M5 40mm Bolt
(2) M5 Washers
(1) M5 Standard or Square Nut
(1) Spring, similar to the dimensions below: ~8.5mm outside diameter
~25mm uncompressed length
~13.8mm fully compressed length

Figure 58: Tensioner spring and bowden connector

## 11. Wiring and Electrical Components

- Wire all components according to the D-Bot Electrical Diagram. (http://www.thingiverse.com/thing:1001065/#files)
- The solid state relay must be bolted to an aluminum rail for heat dissipation.
- Verify jumpers are placed on all pairs of pins under each of the stepper driver boards.
- Leave most wiring loose until all functionality can be confirmed so that fixing and troubleshooting wiring can be done easily.
- Keep low voltage wiring and line voltage AC wiring separate and isolated.
- Wiring which connects to moving components needs to be properly supported so that repeated movement of the wire will not degrade it or cause failures at connections.
- Never rely on solder joints or electrical connectors to secure wiring.
- This instructional video (https://www.youtube.com/watch?v=GkbOJSvhCgU) gives an excellent explanation on the different types of header connectors and how to crimp Dupont connector pins.
- Install the Y and Z endstops with two M3x8mm bolts and two M3 nuts each.
- The best way to secure wiring to the print carriage is to zip-tie wires to the bowden tube or place wiring and bowden tube in a flexible conduit.
- Stepper motor wiring needs to be extended, cover solder splices with heatshrink tubing.
- The hot end heatsink fan is connected to 12V supply power as shown in the diagram. It does not cycle on and off with the part cooling fan because only the negative lead to the part fan is being switched by the microcontroller. The hot end fan will run full time as long as supply power is on.
- An alternative way to wire the endstops is to remove the white connector housing and solder wires directly to the endstop boards.
- If the Ramps cooling fan is connected as shown in the electrical diagram, it will need to have a two pin header soldered to the ramps board. The fan can also be connected to the ramps input power jack.
- Line voltage power jack wiring is shown in the appendix.

## 12. Software Configuration and Initial Set Up

- Connect Arduino/Ramps 1.4 board to PC via USB-B cable. Do not turn on 12v power yet.
- Tune stepper motor drivers using the technique shown here. (https://www.youtube.com/watch?v=GNfKZ7o_7PI) The D-Bot stepper drivers are set to approximately 0.55 volts.
- Download and install Arduino from https://www.arduino.cc/en/Main/Software
- Download D-Bot_Marlin.zip from http://www.thingiverse.com/thing:1001065/#files
- Unzip D-Bot_Marlin.zip
- Open D-Bot_Marlin>Marlin>Marlin.ino
- Set Tools>Board>Mega 2560
- Set Tools>Port> (Change to the COM port used, this may require some trial and error)
- Click verify (checkmark), then upload (arrow).
- If you cannot connect or if you receive a timeout error, you may need to download and install the CH341SER driver. Some Chinese knockoff Arduino boards use a serial chip which is not the same as normal Arduino boards.
- Download Repetier Host from http://www.repetier.com/download-now/ and install, skip the installation of Repetier Server.
- Open Printer Settings and configure per the following 4 pages.

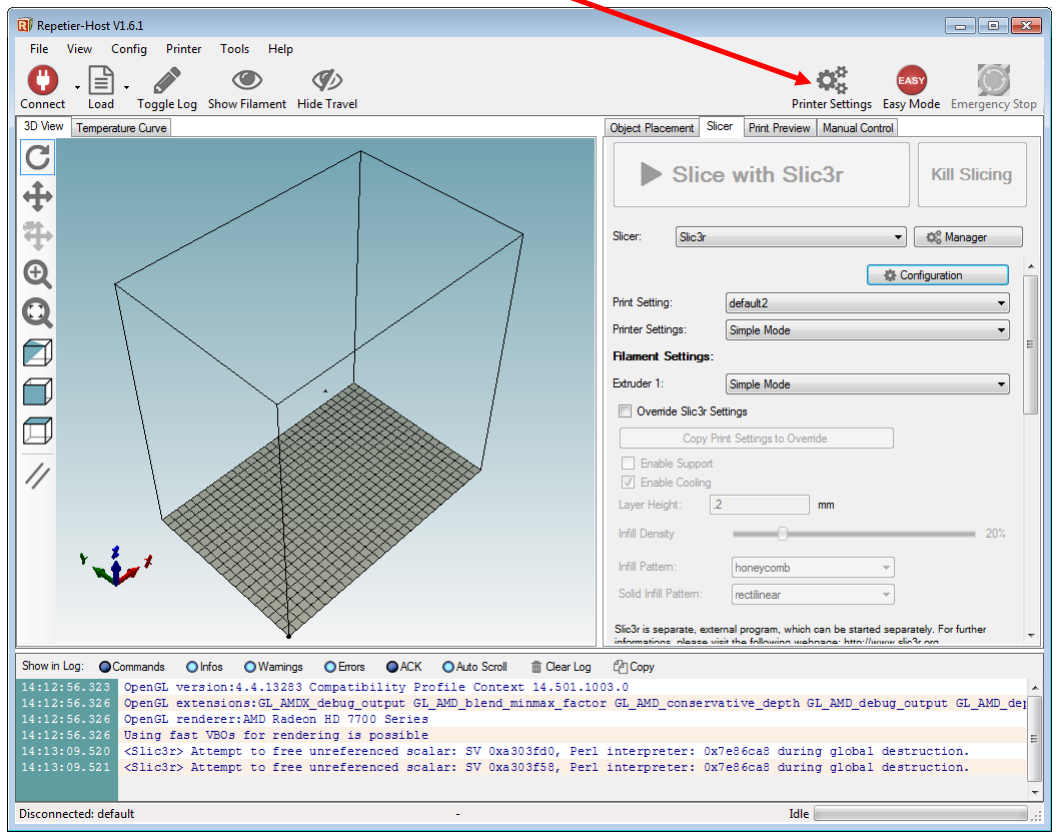
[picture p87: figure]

Repetier Host Settings Page 1 of 4

Set Port to the same COM port used to upload the firmware via Arduino.

Repetier Host Settings Page 2 of 4

Repetier Host Settings Page 3 of 4

Repetier Host Settings Page 4 of 4

Configure Slic3r per the following 9 pages. These settings serve as a good starting point for D-Bot printing. Some settings are required for proper function (bed shape, retract) and some settings can be adjusted based on further testing or based on individual print requirements (infill, layer height, etc).

Slic3r Settings Page 1 of 9

Slic3r Settings Page 2 of 9

Slic3r Settings Page 3 of 9

Slic3r Settings Page 4 of 9

Slic3r Settings Page 5 of 9

Slic3r Settings Page 6 of 9

Slic3r Settings Page 7 of 9

Slic3r Settings Page 8 of 9

Slic3r Settings Page 9 of 9

## 13. Initial Testing

- Turn on the 12v power supply and verify when powered up that the hot end heatsink fan runs and that it does not shut off as long as main power is turned on. If the hot end heatsink fan shuts off at any point then something may be wired incorrectly.
- Click the Connect/Disconnect button to enable communication with the printer. On the Temperature Curve tab of Repetier Host, verify that the Extruder and Bed temperature plots are steady at ambient temperature (between 20C to 25C). If they do not correspond to ambient temperature, thermistor settings may not be correct in configuration.h or thermistors may be wired incorrectly. If the bed or extruder temperature is ramping up without being enabled via Rep Host, something may be wired incorrectly or the Ramps board may be faulty.
- Review the Repetier Host manual control guide to become familiar with the interface and icons http://www.repetier.com/documentation/repetier-host/rhmanual-control/
- Install an M5x40mm bolt in the Z endstop bolt holder and raise the bolt as high as possible to guarantee that the nozzle will not impact into the bed during initial test movements.

- Initial Z endstop calibration and bed leveling:
1. Home the Z axis and make sure that the bed stops several millimeters away from the nozzle. Keep your mouse over the Emergency Stop button in Repetier Host and stop the movement if needed, you don’t want the nozzle to crunch into the glass.
2. Lower the Z endstop bolt by a couple millimeters and home Z. Repeat this process until the nozzle is close to the bed, almost touching. See video demonstration here (https://www.youtube.com/watch?v=HqHSpY42RG0&index=1&list=PLtTX7qAE76Mwo2uvCK9YH6KMR-vQdPqly)
3. Move the print carriage by hand near each corner of the bed and verify distance between nozzle and glass is approximately 0.2mm (thickness of an index card). You should feel slight resistance when an index card is inserted between the nozzle and glass. If you can’t move the XY gantry by hand, click the motor disable button in Rep Host (just left of the P button).
4. Adjust the M3 corner bolt nearest the nozzle to either raise or lower the bed to achieve the correct distance.
5. Repeat for each of the corners, then at each of the four corners again to verify perfect leveling.
6. You should not need to adjust the Z endstop bolt again, all bed leveling and adjustment will be done via the four M3 bed screws.

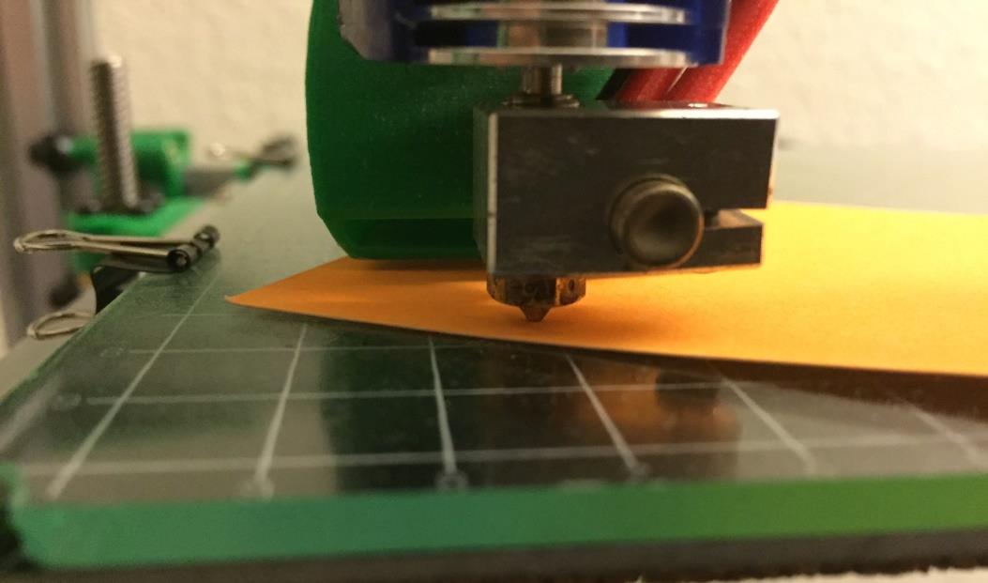
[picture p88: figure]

- Using Repetier Host controls, move all three axes and verify proper direction of movement. If the hot end moves in the wrong direction, wiring or firmware configuration may be incorrect.
(Never disconnect or change control board wiring while the power is on, this includes power supplied via USB cable also.)
- Verify operation of all three endstops, if the hot end or bed moves away from the end stop instead of towards it, a parameter may be wrong in the Rep Host settings or the

Marlin configuration files. The X endstop position can be fine-tuned by adjusting the M3 25mm bolt that points at the X endstop. The nozzle should line up with the left edge of the bed grid when homed.

- If the print carriage is pushed all the way to the back and the Y endstop is activated, the printer will not home to X when commanded. This is an issue with Marlin/ Repetier. Manually push the print carriage away from the Y endstop until the LED turns off before engaging the homing command.
- Calibrate Bowden extrusion steps per this example video. (https://www.youtube.com/watch?v=yLH4K1vNoXo) Extrusion length calculation is in the last half of the video, ignore stepper driver tuning directions, this has already been completed for the D-Bot. When inserting the Bowden tube into the hot end, make sure that the tubing inserts all the way in and is seated into the heatbreak.
- PID Temperature Feedback Tuning:
Proportional Integral Derivative Tuning is an essential step to guarantee proper operation of the temperature feedback loops of both the hot end and the heated bed. Do not skip this step and do not assume that the values preloaded in the configuration file can be reused; each printer derives different PID values based on slight differences in wiring and hardware.

PID tuning - Hot End:
Begin the PID autotune routine for the hot end by typing M303 E0 S200 C8 into the Rep Host G-code interface, then click Send. The nozzle will automatically heat up to 200C and cycle around that set point 8 times then it will cool down.

Once complete, Repetier Host will report three final Kp Ki and Kd values as shown below. Enter these values into the indicated section of the configuration file stored at D-Bot_Marlin>Marlin>configuration.h. Marlin lists these as Ultimaker settings but that is just a default name.

PID tuning – Heated Bed:
Similar to the hot end PID tuning, begin the PID autotune routine for the heated bed by typing M303 E-1 C8 s60 into the Rep Host G-code interface, then click Send. The heated bed will automatically heat up to 60C and cycle around that set point 8 times then it will cool down. This will take several minutes longer for the bed compared to the hot end. Once complete, Repetier Host will report three final Kp Ki and Kd values as shown below. Enter these values into the PIDTEMPBED section of the configuration file stored at D-Bot_Marlin>Marlin>configuration.h. Note: this is not the same section used above, these parameters begin with DEFAULT_bed.

- Once the six parameters for the hot end and bed Kp Ki Kd settings are entered into configuration.h, save the file and close. Reupload D-Bot_Marlin>Marlin>Marlin.ino by using the same process as the initial firmware upload. Rep Host needs to be disconnected (connect/disconnect button under the File menu) or closed completely in order for Arduino to connect to the Mega 2560/Ramps.

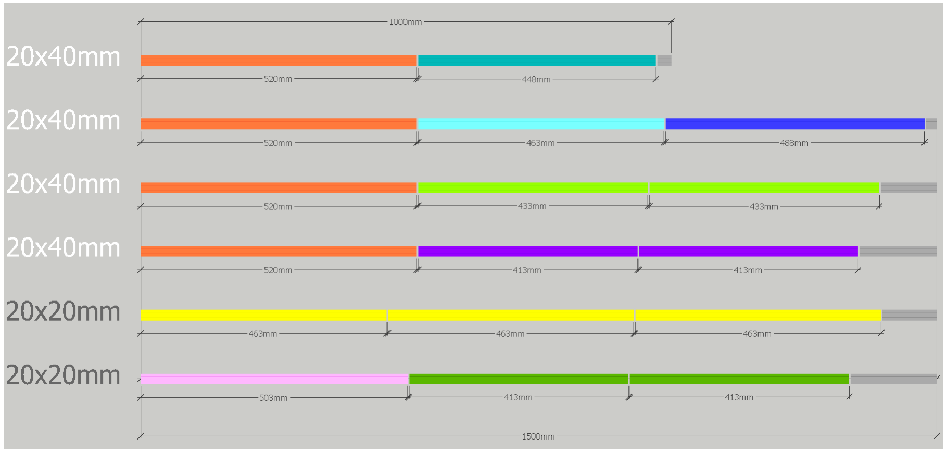
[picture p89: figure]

74

## 14. Appendix

- Railing lengths required for a build based on a 300x300mm bed:

- For a 300x300mm bed, the Z motors will need to be moved forward so that the Z platform is supported at or near the center of gravity for uniform raising and lowering.
- Longer GT2 belts will also be needed for a larger build.
- Line voltage power jack/fuse/switch module wiring is shown below:

Please show your appreciation for this design and all of the volunteer work that went into this documentation by uploading your finished printer to the Thingiverse (http://www.thingiverse.com/thing:1001065/) page and please try to help future builders who may have questions, thank you.

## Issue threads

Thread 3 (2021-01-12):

Stl Units are in Inches

SeanPluemer, 2021-01-12:
Hello, me again!
Figured I would let you know that the stl file units are in inches. Took a bit to get this figured out, when I would load the model up nothing would show up.
I was able to get around this by changing the scale from 100 to 2540 (using PrusaSlicer).

rdudhagra, 2021-01-14:
Should be fixed now, thanks for pointing this out!

Closed 2021-01-14.

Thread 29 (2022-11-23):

Adapt for Polar Robot

hackintoshlover, 2022-11-23:
Hi,
Thanks for the awesome build.
Quick question,
I have modified marlin firmware to adapt polar co-ordinates.
Is the raspberry pi sand table control software compatible with polar co-ordinates instead of cartesian co-ordinates?
Any steps for how to achieve the same?

rdudhagra, 2022-11-26:
Hey!
Should be fairly straightforward. You'll need to modify [`website/server/routes/gcode_controller.js`](https://github.com/rdudhagra/Sand-Table/blob/master/Website/server/routes/gcode_controller.js) slightly to send polar coordinate commands in the format that you'll need and possibly [`process_theta_rho.js`](https://github.com/rdudhagra/Sand-Table/blob/master/Website/server/routes/process_theta_rho.js) if you still want to be able to upload `.thr` track files. Good thing is that `.thr` files are already in polar coordinates so the code in this file will end up being much simpler.

Check out #21 for some more info on switching to a polar coordinate system if you haven't seen that thread yet...I can offer more specific guidelines on what you'd need to change if you have more details on how your modified marlin fw accepts polar coordinates/etc.

hackintoshlover, 2022-12-02:
Hi,
I this for firmware with disabled z-axis.
https://github.com/kory75/Marlin_360

Rest any 3d  printer software works for  control.

hackintoshlover, 2022-12-02:
Hey Ravi,
Will this software work with h-bot setup instead of core-xy?

rdudhagra, 2022-12-07:
Seems like Marlin_360 takes XY coordinates as input so if you're fine with a slightly incorrect preview image on the website (square instead of circular) then I don't think you'll need to make any modifications.

I'm not familiar with an H-Bot setup but from a quick google search it seems compatible. Basically anything that Marlin can do (actually anything that can take GCode commands) will work.

Closed 2022-12-19.

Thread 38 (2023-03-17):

npm install error

jorgeoumier, 2023-03-17:
Hello, i tried now everything what i could find but everytime when i try to start the npm install command i get these errors:
```
> @serialport/bindings@9.0.0 install /home/sepe/Sand-Table/Website/node_modules/@serialport/bindings
> prebuild-install --tag-prefix @serialport/bindings@ || node-gyp rebuild

prebuild-install WARN install No prebuilt binaries found (target=14.8.0 runtime=node arch=arm64 libc= platform=linux)
make: Entering directory '/home/sepe/Sand-Table/Website/node_modules/@serialport/bindings/build'
  CXX(target) Release/obj.target/bindings/src/serialport.o
In file included from ../src/./serialport.h:6,
                 from ../src/serialport.cpp:1:
../../../nan/nan.h: In function ‘void Nan::AsyncQueueWorker(Nan::AsyncWorker*)’:
../../../nan/nan.h:2294:7: warning: cast between incompatible function types from ‘void (*)(uv_work_t*)’ {aka ‘void (*)(uv_work_s*)’} to
uv_after_work_cb’ {aka ‘void (*)(uv_work_s*, int)’} [-Wcast-function-type]
 2294 |     , reinterpret_cast<uv_after_work_cb>(AsyncExecuteComplete)
      |       ^~~~~~~~~~~~~~~~~~~~~~~~~~~~~~~~~~~~~~~~~~~~~~~~~~~~~~~~
../src/serialport.cpp: In function ‘Nan::NAN_METHOD_RETURN_TYPE Open(Nan::NAN_METHOD_ARGS_TYPE)’:
../src/serialport.cpp:78:51: warning: cast between incompatible function types from ‘void (*)(uv_work_t*)’ {aka ‘void (*)(uv_work_s*)’} to ‘uv_after_work_cb’ {aka ‘void (*)(uv_work_s*, int)’} [-Wcast-function-type]
   78 |   uv_queue_work(uv_default_loop(), req, EIO_Open, (uv_after_work_cb)EIO_AfterOpen);
      |                                                   ^~~~~~~~~~~~~~~~~~~~~~~~~~~~~~~
../src/serialport.cpp: In function ‘Nan::NAN_METHOD_RETURN_TYPE Update(Nan::NAN_METHOD_ARGS_TYPE)’:
../src/serialport.cpp:135:53: warning: cast between incompatible function types from ‘void (*)(uv_work_t*)’ {aka ‘void (*)(uv_work_s*)’} to ‘uv_after_work_cb’ {aka ‘void (*)(uv_work_s*, int)’} [-Wcast-function-type]
  135 |   uv_queue_work(uv_default_loop(), req, EIO_Update, (uv_after_work_cb)EIO_AfterUpdate);
      |                                                     ^~~~~~~~~~~~~~~~~~~~~~~~~~~~~~~~~
../src/serialport.cpp: In function ‘Nan::NAN_METHOD_RETURN_TYPE Close(Nan::NAN_METHOD_ARGS_TYPE)’:
../src/serialport.cpp:175:52: warning: cast between incompatible function types from ‘void (*)(uv_work_t*)’ {aka ‘void (*)(uv_work_s*)’} to ‘uv_after_work_cb’ {aka ‘void (*)(uv_work_s*, int)’} [-Wcast-function-type]
  175 |   uv_queue_work(uv_default_loop(), req, EIO_Close, (uv_after_work_cb)EIO_AfterClose);
      |                                                    ^~~~~~~~~~~~~~~~~~~~~~~~~~~~~~~~
../src/serialport.cpp: In function ‘Nan::NAN_METHOD_RETURN_TYPE Flush(Nan::NAN_METHOD_ARGS_TYPE)’:
../src/serialport.cpp:215:52: warning: cast between incompatible function types from ‘void (*)(uv_work_t*)’ {aka ‘void (*)(uv_work_s*)’} to ‘uv_after_work_cb’ {aka ‘void (*)(uv_work_s*, int)’} [-Wcast-function-type]
  215 |   uv_queue_work(uv_default_loop(), req, EIO_Flush, (uv_after_work_cb)EIO_AfterFlush);
      |                                                    ^~~~~~~~~~~~~~~~~~~~~~~~~~~~~~~~
../src/serialport.cpp: In function ‘Nan::NAN_METHOD_RETURN_TYPE Set(Nan::NAN_METHOD_ARGS_TYPE)’:
../src/serialport.cpp:270:50: warning: cast between incompatible function types from ‘void (*)(uv_work_t*)’ {aka ‘void (*)(uv_work_s*)’} to ‘uv_after_work_cb’ {aka ‘void (*)(uv_work_s*, int)’} [-Wcast-function-type]
  270 |   uv_queue_work(uv_default_loop(), req, EIO_Set, (uv_after_work_cb)EIO_AfterSet);
      |                                                  ^~~~~~~~~~~~~~~~~~~~~~~~~~~~~~
../src/serialport.cpp: In function ‘Nan::NAN_METHOD_RETURN_TYPE Get(Nan::NAN_METHOD_ARGS_TYPE)’:
../src/serialport.cpp:314:50: warning: cast between incompatible function types from ‘void (*)(uv_work_t*)’ {aka ‘void (*)(uv_work_s*)’} to ‘uv_after_work_cb’ {aka ‘void (*)(uv_work_s*, int)’} [-Wcast-function-type]
  314 |   uv_queue_work(uv_default_loop(), req, EIO_Get, (uv_after_work_cb)EIO_AfterGet);
      |                                                  ^~~~~~~~~~~~~~~~~~~~~~~~~~~~~~
../src/serialport.cpp: In function ‘Nan::NAN_METHOD_RETURN_TYPE GetBaudRate(Nan::NAN_METHOD_ARGS_TYPE)’:
../src/serialport.cpp:363:58: warning: cast between incompatible function types from ‘void (*)(uv_work_t*)’ {aka ‘void (*)(uv_work_s*)’} to ‘uv_after_work_cb’ {aka ‘void (*)(uv_work_s*, int)’} [-Wcast-function-type]
  363 |   uv_queue_work(uv_default_loop(), req, EIO_GetBaudRate, (uv_after_work_cb)EIO_AfterGetBaudRate);
      |                                                          ^~~~~~~~~~~~~~~~~~~~~~~~~~~~~~~~~~~~~~
../src/serialport.cpp: In function ‘Nan::NAN_METHOD_RETURN_TYPE Drain(Nan::NAN_METHOD_ARGS_TYPE)’:
../src/serialport.cpp:409:52: warning: cast between incompatible function types from ‘void (*)(uv_work_t*)’ {aka ‘void (*)(uv_work_s*)’} to ‘uv_after_work_cb’ {aka ‘void (*)(uv_work_s*, int)’} [-Wcast-function-type]
  409 |   uv_queue_work(uv_default_loop(), req, EIO_Drain, (uv_after_work_cb)EIO_AfterDrain);
      |                                                    ^~~~~~~~~~~~~~~~~~~~~~~~~~~~~~~~
../src/serialport.cpp: At global scope:
../src/serialport.cpp:430:28: warning: unnecessary parentheses in declaration of ‘ToParityEnum’ [-Wparentheses]
  430 | SerialPortParity NAN_INLINE(ToParityEnum(const v8::Local<v8::String>& v8str)) {
      |                            ^
../src/serialport.cpp:449:30: warning: unnecessary parentheses in declaration of ‘ToStopBitEnum’ [-Wparentheses]
  449 | SerialPortStopBits NAN_INLINE(ToStopBitEnum(double stopBits)) {
      |                              ^
In file included from ../../../nan/nan.h:56,
                 from ../src/./serialport.h:6,
                 from ../src/serialport.cpp:1:
/home/sepe/.cache/node-gyp/14.8.0/include/node/node.h:746:7: warning: cast between incompatible function types from ‘void (*)(Nan::ADDON_REGISTER_FUNCTION_ARGS_TYPE)’ {aka ‘void (*)(v8::Local<v8::Object>)’} to ‘node::addon_register_func’ {aka ‘void (*)(v8::Local<v8::Object>, v8::Local<v8::Value>, void*)’} [-Wcast-function-type]
  746 |       (node::addon_register_func) (regfunc),                          \
      |       ^~~~~~~~~~~~~~~~~~~~~~~~~~~~~~~~~~~~~
/home/sepe/.cache/node-gyp/14.8.0/include/node/node.h:780:3: note: in expansion of macro ‘NODE_MODULE_X’
  780 |   NODE_MODULE_X(modname, regfunc, NULL, 0)  // NOLINT (readability/null_usage)
      |   ^~~~~~~~~~~~~
../src/serialport.cpp:483:1: note: in expansion of macro ‘NODE_MODULE’
  483 | NODE_MODULE(serialport, init);
      | ^~~~~~~~~~~
  CXX(target) Release/obj.target/bindings/src/serialport_unix.o
In file included from ../src/serialport.h:6,
                 from ../src/serialport_unix.cpp:2:
../../../nan/nan.h: In function ‘void Nan::AsyncQueueWorker(Nan::AsyncWorker*)’:
../../../nan/nan.h:2294:7: warning: cast between incompatible function types from ‘void (*)(uv_work_t*)’ {aka ‘void (*)(uv_work_s*)’} to
uv_after_work_cb’ {aka ‘void (*)(uv_work_s*, int)’} [-Wcast-function-type]
 2294 |     , reinterpret_cast<uv_after_work_cb>(AsyncExecuteComplete)
      |       ^~~~~~~~~~~~~~~~~~~~~~~~~~~~~~~~~~~~~~~~~~~~~~~~~~~~~~~~
../src/serialport_unix.cpp: In function ‘int setup(int, OpenBaton*)’:
../src/serialport_unix.cpp:176:82: warning: ‘%s’ directive output may be truncated writing up to 1023 bytes into a region of size 1005 [-Wformat-truncation=]
  176 |     snprintf(data->errorString, sizeof(data->errorString), "Error %s Cannot open %s", strerror(errno), data->path);
      |                                                                                  ^~
../src/serialport_unix.cpp:176:13: note: ‘snprintf’ output 20 or more bytes (assuming 1043) into a destination of size 1024
  176 |     snprintf(data->errorString, sizeof(data->errorString), "Error %s Cannot open %s", strerror(errno), data->path);
      |     ~~~~~~~~^~~~~~~~~~~~~~~~~~~~~~~~~~~~~~~~~~~~~~~~~~~~~~~~~~~~~~~~~~~~~~~~~~~~~~~~~~~~~~~~~~~~~~~~~~~~~~~~~~~~~~
../src/serialport_unix.cpp: In function ‘void EIO_Open(uv_work_t*)’:
../src/serialport_unix.cpp:86:84: warning: ‘%s’ directive output may be truncated writing up to 1023 bytes into a region of size 1003 [-Wformat-truncation=]
   86 |     snprintf(data->errorString, sizeof(data->errorString), "Error: %s, cannot open %s", strerror(errno), data->path);
      |                                                                                    ^~
../src/serialport_unix.cpp:86:13: note: ‘snprintf’ output 22 or more bytes (assuming 1045) into a destination of size 1024
   86 |     snprintf(data->errorString, sizeof(data->errorString), "Error: %s, cannot open %s", strerror(errno), data->path);
      |     ~~~~~~~~^~~~~~~~~~~~~~~~~~~~~~~~~~~~~~~~~~~~~~~~~~~~~~~~~~~~~~~~~~~~~~~~~~~~~~~~~~~~~~~~~~~~~~~~~~~~~~~~~~~~~~~~
  CXX(target) Release/obj.target/bindings/src/poller.o
In file included from ../src/poller.cpp:1:
../../../nan/nan.h: In function ‘void Nan::AsyncQueueWorker(Nan::AsyncWorker*)’:
../../../nan/nan.h:2294:7: warning: cast between incompatible function types from ‘void (*)(uv_work_t*)’ {aka ‘void (*)(uv_work_s*)’} to
uv_after_work_cb’ {aka ‘void (*)(uv_work_s*, int)’} [-Wcast-function-type]
 2294 |     , reinterpret_cast<uv_after_work_cb>(AsyncExecuteComplete)
      |       ^~~~~~~~~~~~~~~~~~~~~~~~~~~~~~~~~~~~~~~~~~~~~~~~~~~~~~~~
  CXX(target) Release/obj.target/bindings/src/serialport_linux.o
  SOLINK_MODULE(target) Release/obj.target/bindings.node
  COPY Release/bindings.node
make: Leaving directory '/home/sepe/Sand-Table/Website/node_modules/@serialport/bindings/build'

> node-sass@4.14.1 install /home/sepe/Sand-Table/Website/node_modules/node-sass
> node scripts/install.js

Downloading binary from https://github.com/sass/node-sass/releases/download/v4.14.1/linux-arm64-83_binding.node
Cannot download "https://github.com/sass/node-sass/releases/download/v4.14.1/linux-arm64-83_binding.node":

HTTP error 404 Not Found

Hint: If github.com is not accessible in your location
      try setting a proxy via HTTP_PROXY, e.g.

      export HTTP_PROXY=http://example.com:1234

or configure npm proxy via

      npm config set proxy http://example.com:8080

> sharp@0.25.4 install /home/sepe/Sand-Table/Website/node_modules/sharp
> (node install/libvips && node install/dll-copy && prebuild-install --runtime=napi) || (node-gyp rebuild && node install/dll-copy)

info sharp Downloading https://github.com/lovell/sharp-libvips/releases/download/v8.9.1/libvips-8.9.1-linux-arm64v8.tar.gz

> core-js@3.6.5 postinstall /home/sepe/Sand-Table/Website/node_modules/core-js
> node -e "try{require('./postinstall')}catch(e){}"

Thank you for using core-js ( https://github.com/zloirock/core-js ) for polyfilling JavaScript standard library!

The project needs your help! Please consider supporting of core-js on Open Collective or Patreon:
> https://opencollective.com/core-js
> https://www.patreon.com/zloirock

Also, the author of core-js ( https://github.com/zloirock ) is looking for a good job -)

> node-sass@4.14.1 postinstall /home/sepe/Sand-Table/Website/node_modules/node-sass
> node scripts/build.js
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
rdudhagra, 2023-03-20:
```bash
gyp ERR! stack Error: Command failed: /usr/bin/python -c import sys; print "%s.%s.%s" % sys.version_info[:3];
gyp ERR! stack   File "<string>", line 1
gyp ERR! stack     import sys; print "%s.%s.%s" % sys.version_info[:3];
gyp ERR! stack                       ^
gyp ERR! stack SyntaxError: invalid syntax
```

This seems suspicious to me. What is the output of `/usr/bin/python --version`?

rdudhagra, 2023-04-05:
Hey any luck here?

Closed 2023-04-10.

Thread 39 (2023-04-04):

Problem with the LEDs

PDotStrong, 2023-04-04:
Hi thank you so much for your guide. i struggled a lot but I see light at the end ^^ But now I got Errors like this:

[1] chmod: cannot access '/home/pi/arduino-cli': No such file or directory
[1] /home/sandtable/Documents/Sand-Table/Website/flash-light-strip-controller.sh: line 14: /home/pi/arduino-cli: No such file or directory
[1] /home/sandtable/Documents/Sand-Table/Website/flash-light-strip-controller.sh: line 17: /home/pi/arduino-cli: No such file or directory
[1] /home/sandtable/Documents/Sand-Table/Website/flash-light-strip-controller.sh: line 25: /home/pi/arduino-cli: No such file or directory
[1] /home/sandtable/Documents/Sand-Table/Website/flash-light-strip-controller.sh: line 29: /home/pi/arduino-cli: No such file or directory
[1] Server (production) is listening on port 3000

^^

and I cant change the LED to a static light?!?

rdudhagra, 2023-04-04:
Hmm seems like my LED strip uploading script failed to install `arduino-cli`.
Two things to try:
1. Can you try running `flash-light-strip-controller.sh` in the `Website` folder manually?
2. Run the following commands to install `arduino-cli` (taken directly from the above script)?
```bash
curl -fsSL https://raw.githubusercontent.com/arduino/arduino-cli/master/install.sh | BINDIR=/home/pi/ sh
chmod +x /home/pi/arduino-cli
```

Let me know if it still doesn't work after doing both of those.

PDotStrong, 2023-04-05:
I tried the first Solution and got:

sandtable@raspberrypi:~/Documents/Sand-Table/Website $ sh flash-light-strip-controller.sh
arduino-cli not found! Installing...
/home/pi/ ($BINDIR) folder not found. Please create it before continuing.
Failed to install arduino-cli
chmod: cannot access '/home/pi/arduino-cli': No such file or directory
flash-light-strip-controller.sh: 14: /home/pi/arduino-cli: not found
flash-light-strip-controller.sh: 17: /home/pi/arduino-cli: not found
flash-light-strip-controller.sh: 22: cd: can't cd to flash-light-strip-controller.sh
flash-light-strip-controller.sh: 25: /home/pi/arduino-cli: not found
flash-light-strip-controller.sh: 28: source: not found
flash-light-strip-controller.sh: 29: /home/pi/arduino-cli: not found
Done!

Second Solution:

sandtable@raspberrypi:~ $ cd ~/Documents/Sand-Table/Website
sandtable@raspberrypi:~/Documents/Sand-Table/Website $ curl -fsSL https://raw.githubusercontent.com/arduino/arduino-cli/master/install.sh | BINDIR=/home/pi/ sh
od +x /home/pi/arduino-cli/home/pi/ ($BINDIR) folder not found. Please create it before continuing.
Failed to install arduino-cli
sandtable@raspberrypi:~/Documents/Sand-Table/Website $ chmod +x /home/pi/arduino-cli
chmod: cannot access '/home/pi/arduino-cli': No such file or directory
sandtable@raspberrypi:~/Documents/Sand-Table/Website $

No change =(

PDotStrong, 2023-04-05:
I tried to create the missing directory but now i got this:

sandtable@raspberrypi:~ $ sudo mkdir /home/pi
sandtable@raspberrypi:~ $ curl -fsSL https://raw.githubusercontent.com/arduino/arduino-cli/master/install.sh | BINDIR=/home/pi/ sh
Installing in /home/pi/
ARCH=ARMv7
OS=Linux
Using curl as download tool
Downloading https://downloads.arduino.cc/arduino-cli/arduino-cli_0.31.0_Linux_ARMv7.tar.gz
cp: cannot create regular file '/home/pi/arduino-cli': Permission denied
Failed to install arduino-cli

PDotStrong, 2023-04-05:
is it possible that I installed everything in wrong directorys? because I find often the path /home/pi/ or /home/pi/Documents... or must I change Pi to my raspberry name like sandtable

PDotStrong, 2023-04-05:
I solved the problem! Thank you

PDotStrong, 2023-04-05:
I still have the problem, when I want to fix a static color, I got anything else =/

rdudhagra, 2023-04-05:
Hmm ok not sure if I fully follow...
If `arduino-cli` is still giving you problems, my guess is it's a permissions issue. So try running:
```bash
sudo chown -R pi:pi /home/pi
sudo chmod -R 755 /home/pi
```
(source: https://forums.raspberrypi.com/viewtopic.php?t=177135)

You shouldn't need to change your Pi's hostname.

rdudhagra, 2023-04-05:
OOOOH I see what the issue is. Your username is `sandtable`, not `pi`. So my scripts assume the latter username and I guess that broke things. So you could either rename your user or just change all references of `/home/pi` in the code to `/home/sandtable`.

rdudhagra, 2023-04-05:
The only instances that I can find for the username change are in `flash-light-strip-controller.sh` in the `Website` folder and `start.sh` in the same folder (which I mentioned in #40).

PDotStrong, 2023-04-18:
Update: I think I find a problem, my Leds strips ar sk6812 and that are rgbw leds and so not direct supported from fastled right? Can you help me?

PDotStrong, 2023-04-26:
Hi I tried now a rgb led strip but there are also strange thing happen. Is it possible to run my rgbw led strip ? Or i have to use a rgb led strip? I looking for a nice solutions =) that is my last issue before I can finisch the table =S

rdudhagra, 2023-04-26:
You may have to do some googling but any LED strip that's supported by the `FastLED` Arduino library will work!

PDotStrong, 2023-04-27:
I find out that my LED RGBW are not supported from FastLED only with a work over, so I bought an LED RGB WS2813 5050 5V with DI/DO Bi/Bo so exact the same like yours?!? But I only get a red flashing light strip =/ I´m almost lost with it... Spend so much time now for no steps further :,(

rdudhagra, 2023-04-27:
WS2813 should work. Can you send me a video of the LEDs and lots of detailed images of your wiring?

PDotStrong, 2023-04-28:
Hi I found the problm with the RGB Stripes. i wired the LED Stripes like your circuit diagrams and that was not possible because the Digital Pin of the Arduino and the LED have not the same ground and produced my issues.

PDotStrong, 2023-05-04:
Hi, I changed the rgbw trough rgb stripes 2 x 1 meter stripes with 60 leds

set it uo in the arduino and uploaded it and it works, bit when I connect everything raspberry etc the only one strip shine?!? What could be the reason?

PDotStrong, 2023-05-04:
Hi, I changed the rgbw trough rgb stripes 2 x 1 meter stripes with 60 leds each

set it in the arduino and uploaded it and it works connected only to the arduino and pc, but when I connect everything raspberry etc the only one strip shine?!? What could be the reason?

rdudhagra, 2023-05-05:
Can you send pictures + a wiring diagram for your setup?

PDotStrong, 2023-05-05:
I will send you all combination I tried :)
On Monday I will send you everything !

thank you so much for your help! :)

Closed 2023-05-08.

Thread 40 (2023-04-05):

auto start of the server doesnt work

PDotStrong, 2023-04-05:
Hi, Im again =)

I followed you guide and see the web app start tracks etc but when I tried to set the auto start for the web server i got errors like follow:

sandtable@sandtable:~/Documents/Sand-Table/Website $ cd
sandtable@sandtable:~ $ sudo nano /etc/systemd/system/sandtable.service
sandtable@sandtable:~ $ sudo systemctl start sandtable.service
sandtable@sandtable:~ $ sudo systemctl status sandtable.service
● sandtable.service - Runs sand table webserver
     Loaded: loaded (/etc/systemd/system/sandtable.service; disabled; vendor preset: enabled)
     Active: failed (Result: exit-code) since Wed 2023-04-05 12:49:49 BST; 23s ago
    Process: 1981 ExecStart=/home/sandtable/Documents/Sand-Table/Website/start.sh (code=exited, status=>   Main PID: 1981 (code=exited, status=127)
        CPU: 15ms

Apr 05 12:49:49 sandtable systemd[1]: sandtable.service: Scheduled restart job, restart counter is at 5.Apr 05 12:49:49 sandtable systemd[1]: Stopped Runs sand table webserver.
Apr 05 12:49:49 sandtable systemd[1]: sandtable.service: Start request repeated too quickly.
Apr 05 12:49:49 sandtable systemd[1]: sandtable.service: Failed with result 'exit-code'.
Apr 05 12:49:49 sandtable systemd[1]: Failed to start Runs sand table webserver.
lines 1-12/12 (END)

and this time I dont understand what I can do alone =/

Im so near to reach the goal ;-(

rdudhagra, 2023-04-05:
Hmm something is erroring when you run the web server. Can you, from the `Website` folder, run `npm run prod` and post the output? If running that command launches the web server then something is fishy with the systemd service.

rdudhagra, 2023-04-05:
Although changing `/home/pi` to `/home/sandtable` like in #39 may also solve this issue. Specifically in `start.sh` in the `Website` folder

PDotStrong, 2023-04-06:
Hi!

I change all pi´s to sandtable but still this:

sandtable@sandtable:~ $ sudo systemctl status sandtable.service
● sandtable.service - Runs sand table webserver
     Loaded: loaded (/etc/systemd/system/sandtable.service; disabled; vendor preset: enabled)
     Active: failed (Result: exit-code) since Thu 2023-04-06 06:02:40 BST; 5s ago
    Process: 2119 ExecStart=/home/sandtable/Documents/Sand-Table/Website/start.sh (code=exited, status=127)
   Main PID: 2119 (code=exited, status=127)
        CPU: 13ms

Apr 06 06:02:40 sandtable systemd[1]: sandtable.service: Scheduled restart job, restart counter is at 5.
Apr 06 06:02:40 sandtable systemd[1]: Stopped Runs sand table webserver.
Apr 06 06:02:40 sandtable systemd[1]: sandtable.service: Start request repeated too quickly.
Apr 06 06:02:40 sandtable systemd[1]: sandtable.service: Failed with result 'exit-code'.
Apr 06 06:02:40 sandtable systemd[1]: Failed to start Runs sand table webserver.
sandtable@sandtable:~ $ cd ~/Documents/Sand-Table/Website/
sandtable@sandtable:~/Documents/Sand-Table/Website $ sudo systemctl start sandtable.service
sandtable@sandtable:~/Documents/Sand-Table/Website $ sudo systemctl status sandtable.service
● sandtable.service - Runs sand table webserver
     Loaded: loaded (/etc/systemd/system/sandtable.service; disabled; vendor preset: enabled)
     Active: failed (Result: exit-code) since Thu 2023-04-06 06:03:10 BST; 2s ago
    Process: 2147 ExecStart=/home/sandtable/Documents/Sand-Table/Website/start.sh (code=exited, status=127)
   Main PID: 2147 (code=exited, status=127)
        CPU: 13ms

Apr 06 06:03:10 sandtable systemd[1]: sandtable.service: Scheduled restart job, restart counter is at 5.
Apr 06 06:03:10 sandtable systemd[1]: Stopped Runs sand table webserver.
Apr 06 06:03:10 sandtable systemd[1]: sandtable.service: Start request repeated too quickly.
Apr 06 06:03:10 sandtable systemd[1]: sandtable.service: Failed with result 'exit-code'.
Apr 06 06:03:10 sandtable systemd[1]: Failed to start Runs sand table webserver.

I hope for a good tip =)

The server itself is fine, I can reach the Website and change LED modes ( still no useable static change =/) and Tracks are importable and playable. Only the autostart of the server doesnt work =/

here the code when i start the npm run prod in the website folder:

sandtable@sandtable:~/Documents/Sand-Table/Website $ npm run prod

> sandtable@1.0.0 prod /home/sandtable/Documents/Sand-Table/Website
> rm -rf dist && npm run build && export NODE_ENV=production && concurrently "npm run react" "node dist/app.js"

> sandtable@1.0.0 build /home/sandtable/Documents/Sand-Table/Website
> babel server -d dist
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
rdudhagra, 2023-04-10:
Ah I see what the issue is. I want to see what the website process itself's output is...can you try restarting the systemd service again and looking through the output of `journalctl -xe` for the relevant log lines?

rdudhagra, 2023-04-11:
So open two terminals...
In the first, run: `journalctl -xe`. It'll spam out all the systemctl logs that you get on the Pi.
In a second terminal, run `sudo systemctl restart sandtable.service`.

You should see output in the first terminal relating to the sand table—post that output here and I'll take a look.

PDotStrong, 2023-04-24:
journal:

sandtable@sandtable:~ $ journalctl -xe
░░ Subject: A start job for unit sandtable.service has failed
░░ Defined-By: systemd
░░ Support: https://www.debian.org/support
░░
░░ A start job for unit sandtable.service has finished with a failure.
░░
░░ The job identifier is 1972 and the job result is failed.
Apr 24 06:03:28 sandtable systemd[1]: Starting Cleanup of Temporary Directories...
░░ Subject: A start job for unit systemd-tmpfiles-clean.service has begun execution
░░ Defined-By: systemd
░░ Support: https://www.debian.org/support
░░
░░ A start job for unit systemd-tmpfiles-clean.service has begun execution.
░░
░░ The job identifier is 2040.
Apr 24 06:03:28 sandtable systemd[1]: systemd-tmpfiles-clean.service: Succeeded.
░░ Subject: Unit succeeded
░░ Defined-By: systemd
░░ Support: https://www.debian.org/support
░░
░░ The unit systemd-tmpfiles-clean.service has successfully entered the 'dead' state.
Apr 24 06:03:28 sandtable systemd[1]: Finished Cleanup of Temporary Directories.
░░ Subject: A start job for unit systemd-tmpfiles-clean.service has finished successfully
░░ Defined-By: systemd
░░ Support: https://www.debian.org/support
░░
░░ A start job for unit systemd-tmpfiles-clean.service has finished successfully.
░░
░░ The job identifier is 2040.
lines 3384-3412/3412 (END)

server :

sandtable@sandtable:~/Documents/Sand-Table/Website $ sudo systemctl restart sandtable.service
sandtable@sandtable:~/Documents/Sand-Table/Website $ sudo systemctl status sandtable.service
● sandtable.service - Runs sand table webserver
     Loaded: loaded (/etc/systemd/system/sandtable.service; disabled; vendor preset: enabled)
     Active: failed (Result: exit-code) since Mon 2023-04-24 06:02:50 BST; 1min 7s ago
    Process: 2642 ExecStart=/home/sandtable/Documents/Sand-Table/Website/start.sh (code=exited, status=127)
   Main PID: 2642 (code=exited, status=127)
        CPU: 15ms

Apr 24 06:02:50 sandtable systemd[1]: sandtable.service: Scheduled restart job, restart counter is at 5.
Apr 24 06:02:50 sandtable systemd[1]: Stopped Runs sand table webserver.
Apr 24 06:02:50 sandtable systemd[1]: sandtable.service: Start request repeated too quickly.
Apr 24 06:02:50 sandtable systemd[1]: sandtable.service: Failed with result 'exit-code'.
Apr 24 06:02:50 sandtable systemd[1]: Failed to start Runs sand table webserver.
sandtable@sandtable:~/Documents/Sand-Table/Website $

PDotStrong, 2023-04-26:
Solved, found a wrong path for the start

Closed 2023-04-26.

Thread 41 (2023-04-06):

Is it possible to change the design ob the website? like color? or put in a background?

PDotStrong, 2023-04-06:
I like the Website easy and comfortable. I only want to change the Background to maybe a cool pic. Is this possible? and if yes where i have to look up =)

Sry for all the stupid questions xD but Im very new to arduinos Raspberrys and co

rdudhagra, 2023-04-10:
Yea this should be possible. You'll have to look up how the React.js framework works but it should theoretically be a simple modification to `Website/src/app/index.jsx`

PDotStrong, 2023-04-28:
I found how I can change the Text of everything in the app but everything that seems to be color doesnt change anything if I changed the values xD is it really only the index.jsx?

rdudhagra, 2023-04-28:
Might be another file, possibly one of the `.scss` files.

PDotStrong, 2023-04-28:
I try it and keep you up to date :)

Closed 2023-05-04.

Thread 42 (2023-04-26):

Problem with Gantry and/ or sensorless homing

PDotStrong, 2023-04-26:
I changed the size of the ganrty in the .env file in 500x500 mm but at start it moved always on new spots an the carrier stops never in the middle. How shoild the gantry / carrier behave at server start?

and sry xD for alle issues

rdudhagra, 2023-04-26:
haha no worries! So when you turn the table on:
(1) The gantry will move all the way to the left on one axis
(2) The gantry will move all the way down on the other axis
(3) The gantry will move diagonally to the center of the table

Since your table is a different size from mine you'll need to change the dimensions in `.env` as you mentioned AND reflash the Marlin firmware with the new dimensions (you'll have to modify `Configuration.h`, specifically [these lines](https://github.com/rdudhagra/Sand-Table/blob/f8876251e55bee3187eb94d0f94dd297293fad03/Marlin-2.0.x/Marlin/Configuration.h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)).

PDotStrong, 2023-04-27:
Hi :) I changed the size on your mentioned spots, but nothing changed really… I will check the hardware for sensorless homing again…  Video is made

PDotStrong, 2023-04-27:
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

PDotStrong, 2023-04-27:
![Uploading image.jpg…]()

PDotStrong, 2023-04-27:
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

PDotStrong, 2023-04-27:
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

PDotStrong, 2023-04-27:
https://user-images.githubusercontent.com/129870639/234777829-ea4fcb3a-b8f5-4ee5-8cdf-293d84c7512f.mov

PDotStrong, 2023-04-27:
I got it! THANK YOU =)

PDotStrong, 2023-05-08:
When i change the parametrs in configuration.h and uploaded it and the change the values of x and y in the .env files. have I something to make that the change get refreshed in the machine?

rdudhagra, 2023-05-11:
Not sure what you mean exactly but you do need to restart the webserver to refresh changes in `.env`.

Closed 2023-05-11.

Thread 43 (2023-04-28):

Drawn Tracks are wrong

PDotStrong, 2023-04-28:
Next Problem ^^

I tried to create own Sand Pics on Sandify.org and put in my machine values (470x510) and when i upload these files in the machine it draw only oin 1/3 of the area =/ but why? I changed the values in .env and marlin and the homing works fine.

also when I use the button fit the pic get bigger but not enough to fill the hole area.

i tried sand pic from thers but these are too big for my area and it crashed in the walls so i tried fit these pic but doesnt work =/

maybe I´m blind but can you help^^
How you create your Tracks? Also sandify or something else? The size of the table is changed in .env and marlin and I also sudo daemon-reload to refresh everything? And the homing works .

PDotStrong, 2023-04-28:
Also you have Track that are bigger then your table size, if I use bigger track from the internet my Carrier crash in the boarders and that are not right or?

rdudhagra, 2023-04-28:
Are you exporting as `gcode` or `thr`? The polar files' radius values go from 0 to 1 (unless something changed and I'm mistaken now) and my website will convert them based on the size of your table.

The table should not crash into the borders of the table since Marlin has "software endstops" that will limit how far the gantry is allowed to go.

(you might have your X and Y axes flipped?)

PDotStrong, 2023-04-28:
It should not wrong axis because the center is right from the dimension … hopefully xD

I upload .thr files in the app and export as .thr files from sandify - it works but to small

hmm ok, for my gantry is it possible… dammit

I you the marlin file from your guide. And the homing make what you discribed

PDotStrong, 2023-04-28:
I didnt change the motherboard value in marlin, could this be the problem? I have a ramps 1.4 board instaed your 1.6

could that be the readon for my issues with the unbound system an track that are to small?

PDotStrong, 2023-04-29:
Is it a problem, that I have a rectangle machine configured in sandify and export the file as thr? I found so much points where I dont know what I have to fix, that I got finally a finished table . I hope you can give me hints / guide that I reach my goal :)

rdudhagra, 2023-04-29:
RAMPS 1.4 should be fine. Can you send me your .thr file and the .gcode file that the server generates when you uploaded the .thr file?

rdudhagra, 2023-05-05:
If it's not too much work to send them over—might be something about how sandify generates tracks that I'm not aware of.

PDotStrong, 2023-05-05:
I will create you the files On Monday !

thank you so much for your help! :)

Closed 2023-05-11.

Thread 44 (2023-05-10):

npm installation error

marcoeli007, 2023-05-10:
Hello, during npm installation get these errors:

npm` ERR! code 1
npm ERR! path /mnt/dietpi_userdata/Website/node_modules/@serialport/bindings
npm ERR! command failed
npm ERR! command sh -c prebuild-install --tag-prefix @serialport/bindings@ || node-gyp rebuild
npm ERR! gyp info it worked if it ends with ok
npm ERR! gyp info using node-gyp@3.8.0
npm ERR! gyp info using node@20.1.0 | linux | arm64
npm ERR! gyp ERR! configure error
npm ERR! gyp ERR! stack Error: Command failed: /usr/bin/python -c import sys; print "%s.%s.%s" % sys.version_info[:3];
npm ERR! gyp ERR! stack   File "<string>", line 1
npm ERR! gyp ERR! stack     import sys; print "%s.%s.%s" % sys.version_info[:3];
npm ERR! gyp ERR! stack                       ^
npm ERR! gyp ERR! stack SyntaxError: invalid syntax
npm ERR! gyp ERR! stack
npm ERR! gyp ERR! stack     at ChildProcess.exithandler (node:child_process:419:12)
npm ERR! gyp ERR! stack     at ChildProcess.emit (node:events:511:28)
npm ERR! gyp ERR! stack     at maybeClose (node:internal/child_process:1098:16)
npm ERR! gyp ERR! stack     at Socket.<anonymous> (node:internal/child_process:456:11)
npm ERR! gyp ERR! stack     at Socket.emit (node:events:511:28)
npm ERR! gyp ERR! stack     at Pipe.<anonymous> (node:net:335:12)
npm ERR! gyp ERR! System Linux 6.1.21-v8+
npm ERR! gyp ERR! command "/usr/local/bin/node" "/mnt/dietpi_userdata/Website/node_modules/.bin/node-gyp" "rebuild"
npm ERR! gyp ERR! cwd /mnt/dietpi_userdata/Website/node_modules/@serialport/bindings
npm ERR! gyp ERR! node -v v20.1.0
npm ERR! gyp ERR! node-gyp -v v3.8.0
npm ERR! gyp ERR! not ok_

Installation:
- RP3
- Python 3.9.2
- npn 9.6.6
- nvm 0.39.3

Thanks for your help!

rdudhagra, 2023-05-11:
What version of node do you have installed? It should be `14.8.0`. See https://github.com/rdudhagra/Sand-Table/tree/master/Build%20Guide#raspberry-pi-setupwebserver-installation if you haven't already.

marcoeli007, 2023-05-11:
Thanks! It works after changing the version. I probably got it mixup during the initial installation...

Closed 2023-05-19.

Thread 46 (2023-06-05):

Question Autostart

PDotStrong, 2023-06-05:
Hi I am again 🙈

last question so far! Is it possible to start with a specific tracklist, so that after restart or plug in the system automatically start tracks? Where I have to make it?

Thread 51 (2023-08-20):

getting Command failed: /usr/bin/python -c import sys error while running npm install

McReeii, 2023-08-20:

McReeii, 2023-08-20:
I just had to install Python-2, new raspberry image comes pre-install with Python-3

Closed 2023-08-20.

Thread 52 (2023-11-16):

Using with grbl

hackintoshlover, 2023-11-16:
Hi Ravi,
Wanted to use the device with grbl firmware instead of marlin.
All the codes are almost similar except marlin uses g28 for homing and grbl uses $h.
Where should i make changes in the code so that it parse $h on bootup.
Rigjt now when the raspberry pi boots up and loads the server, my table homes automatically.
So i assume its send g28 for marlin, i want to send $h instead.
Kindly help.

rdudhagra, 2023-11-16:
Hey! Take a look at https://github.com/rdudhagra/Sand-Table/blob/master/Website/server/routes/gcode_controller.js (Line 352). You'll have to modify that line to match what grbl is looking for (and perhaps the subsequent Marlin-specific commands as well).

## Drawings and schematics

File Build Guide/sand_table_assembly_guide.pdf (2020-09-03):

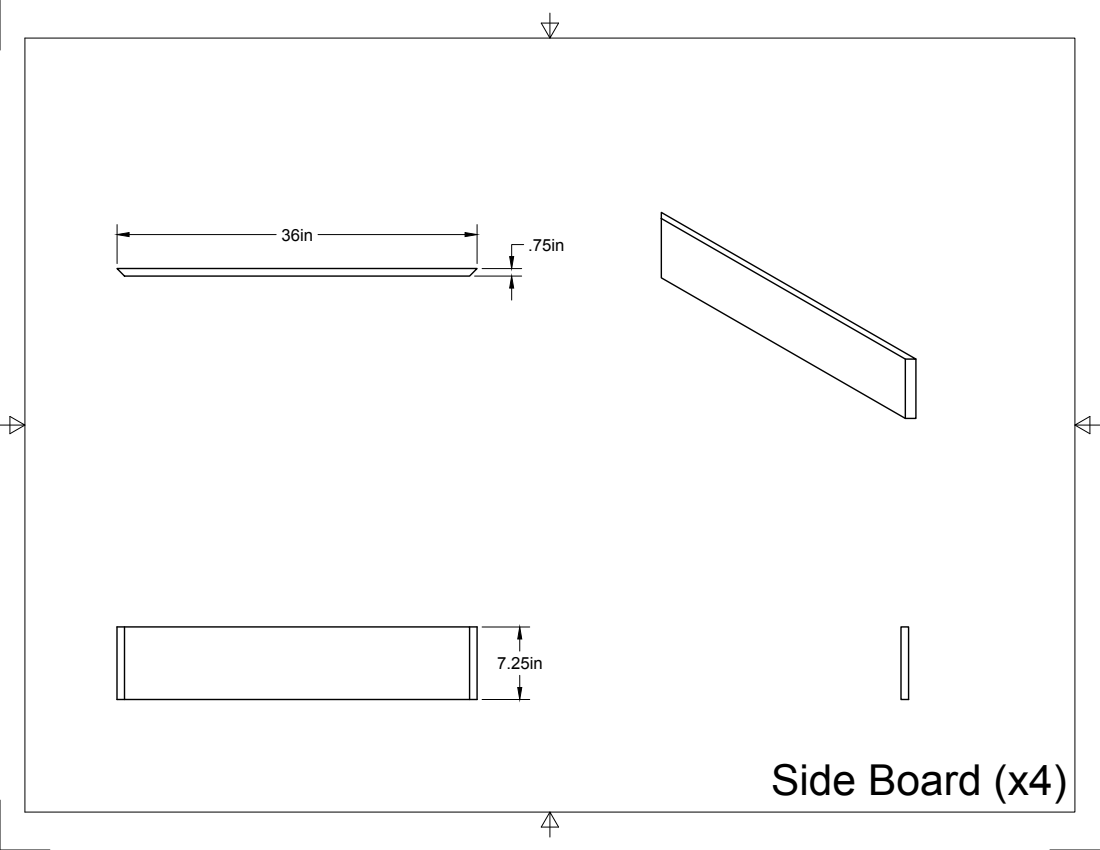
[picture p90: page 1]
Side Board (x4)

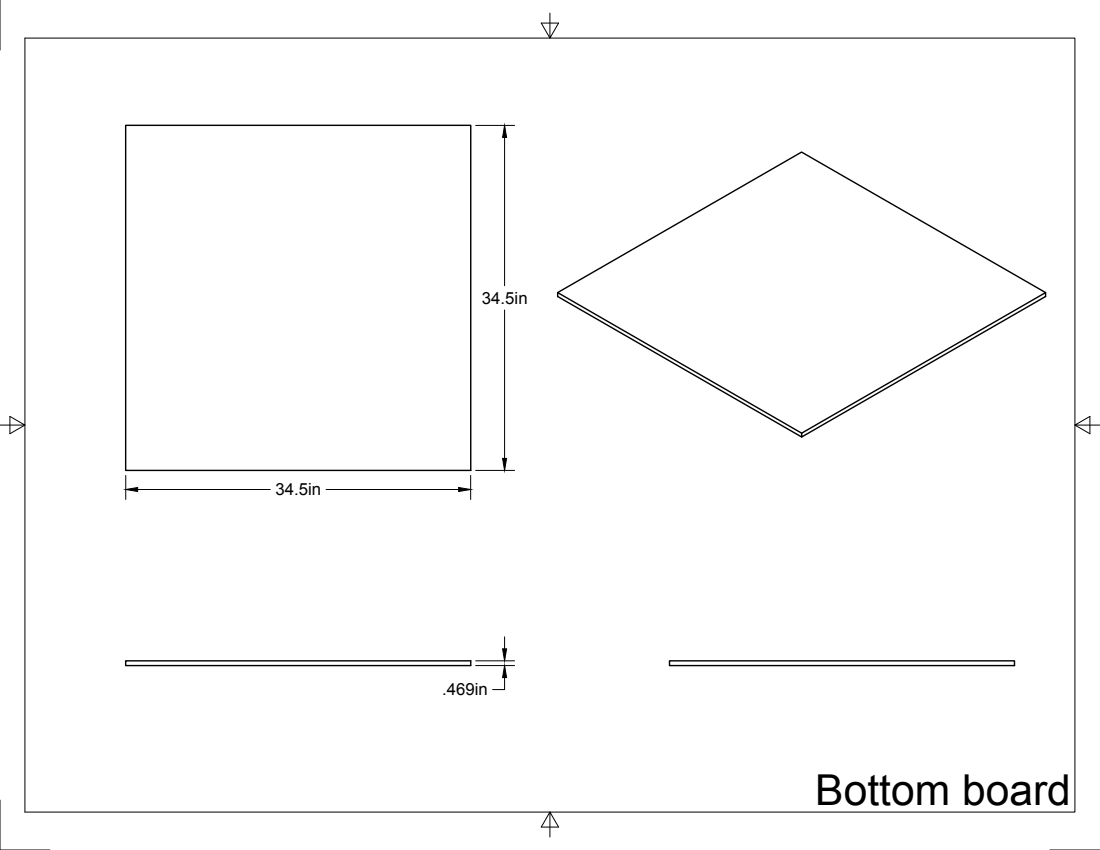
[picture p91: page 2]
Bottom board

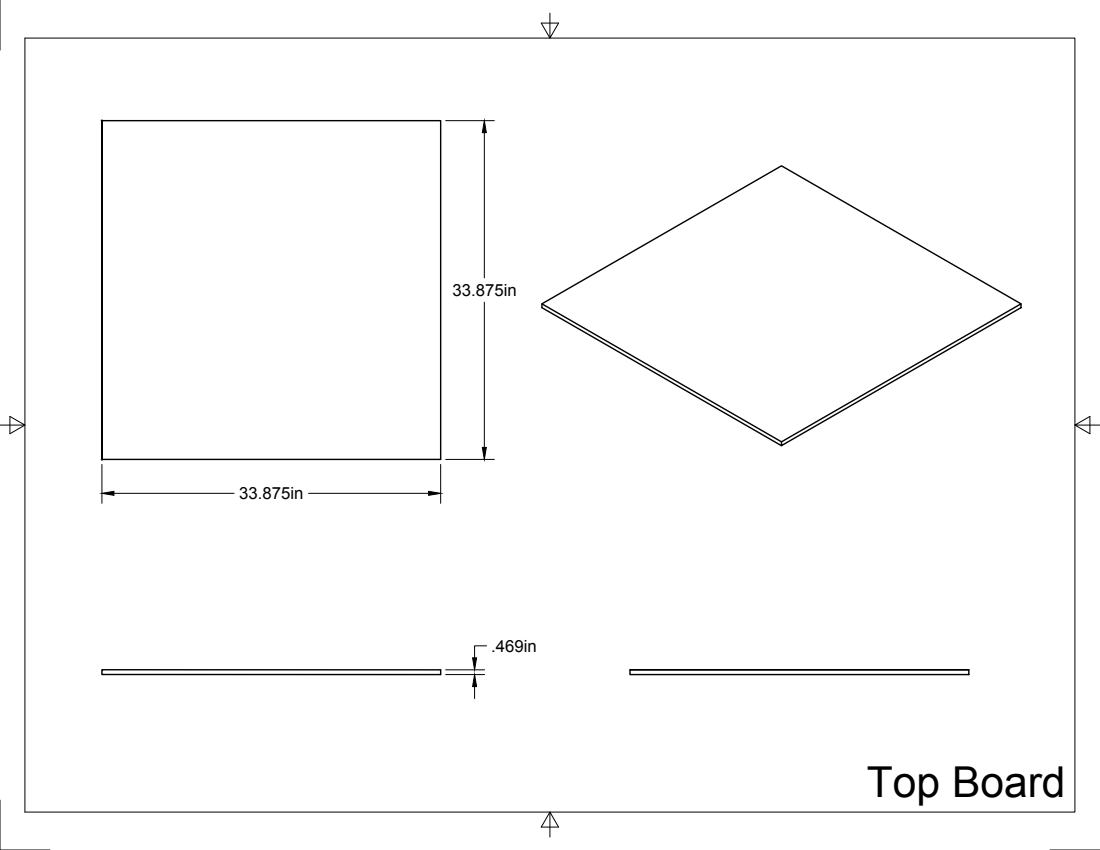
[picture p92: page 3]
Top Board

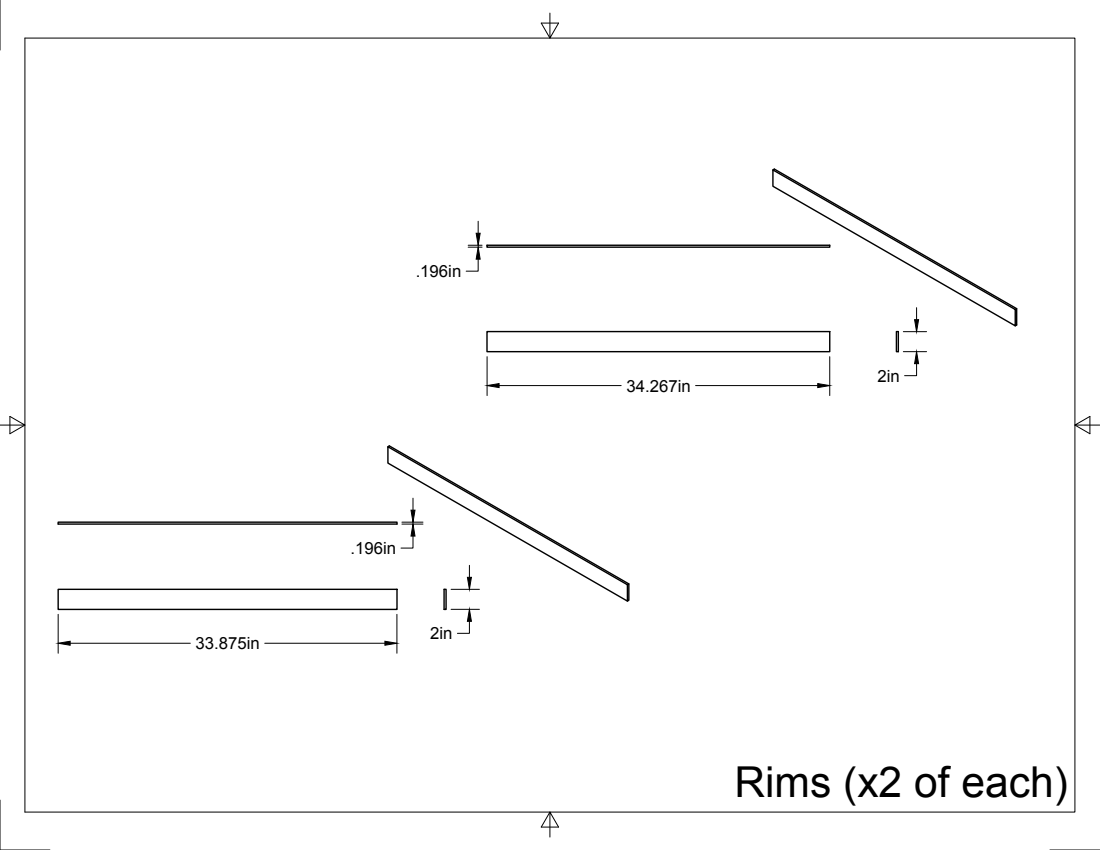
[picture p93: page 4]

Rims (x2 of each)

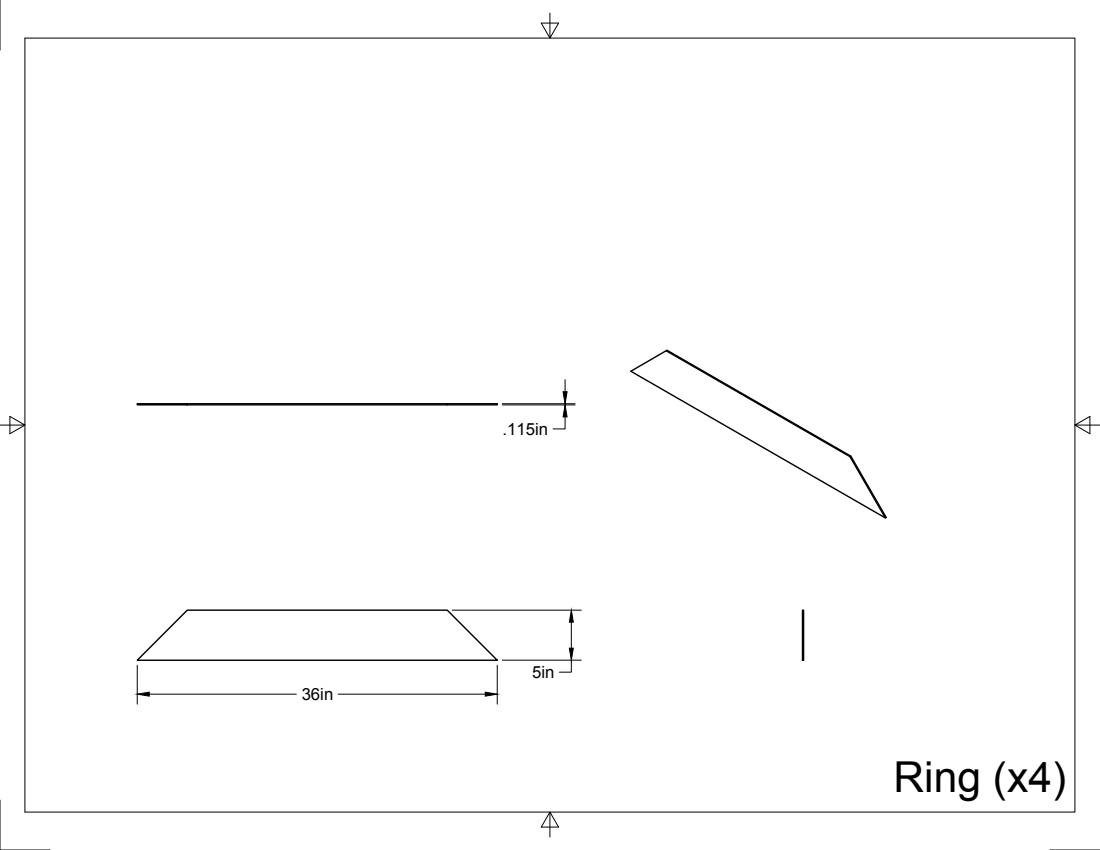
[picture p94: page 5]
Ring (x4)

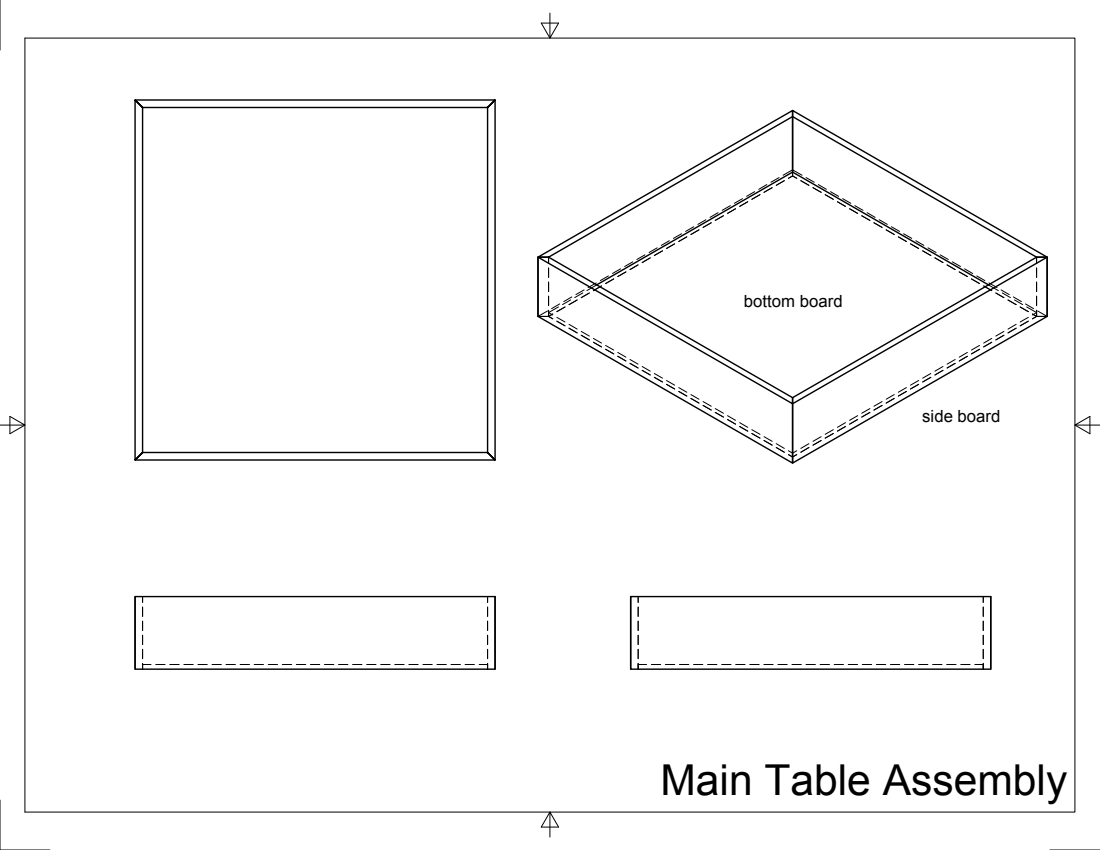
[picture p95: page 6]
bottom board; side board

Main Table Assembly

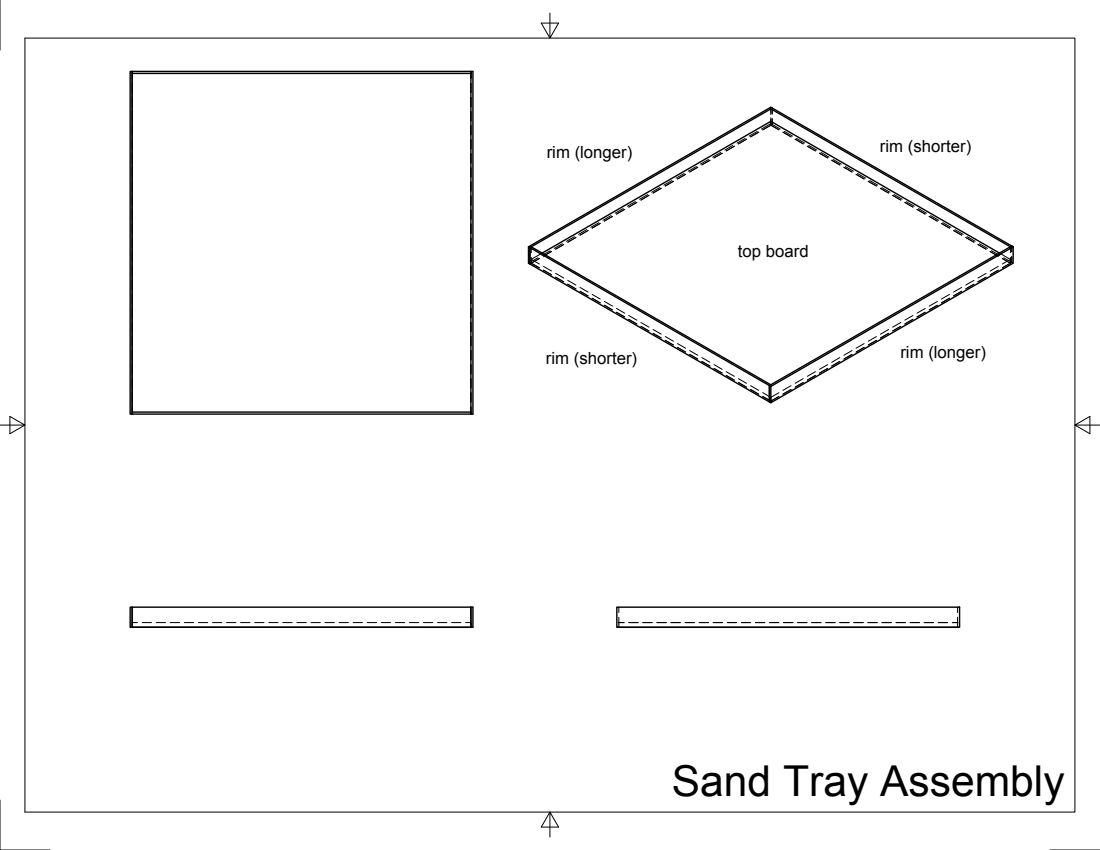
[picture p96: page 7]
top board; rim (longer); rim (shorter)

Sand Tray Assembly

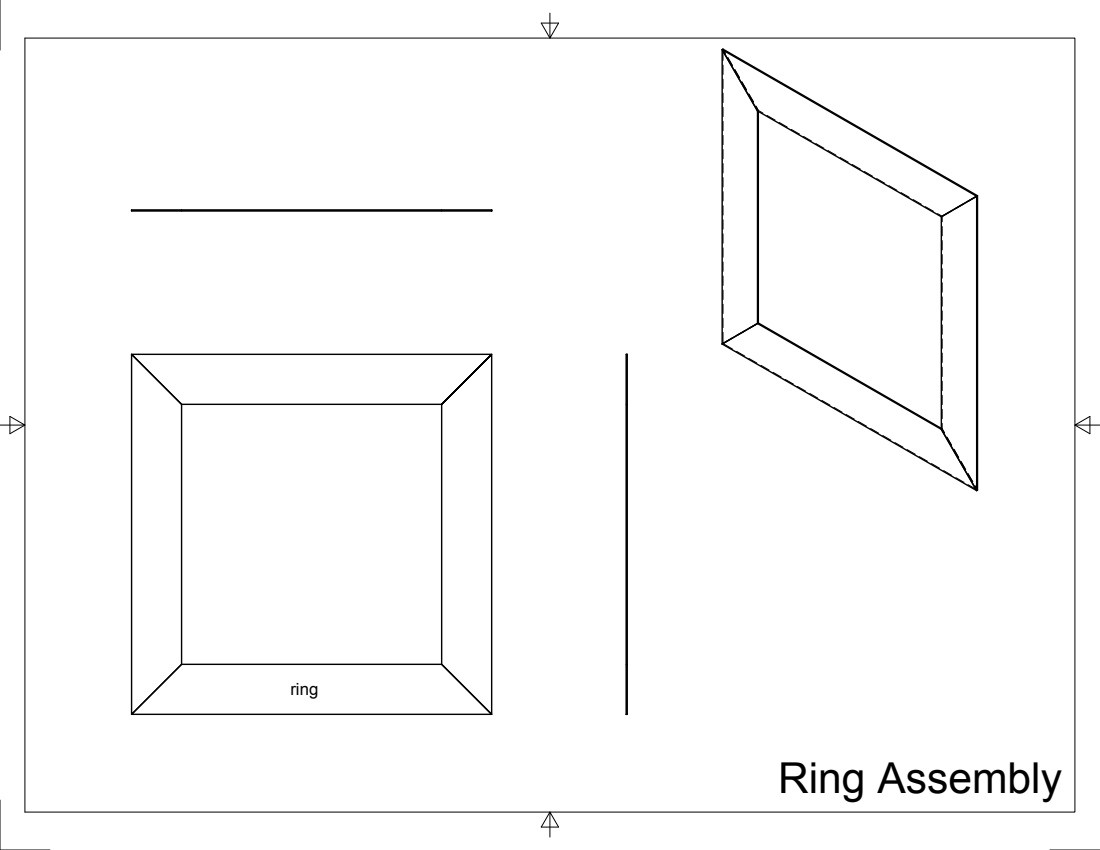
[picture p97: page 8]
Ring Assembly

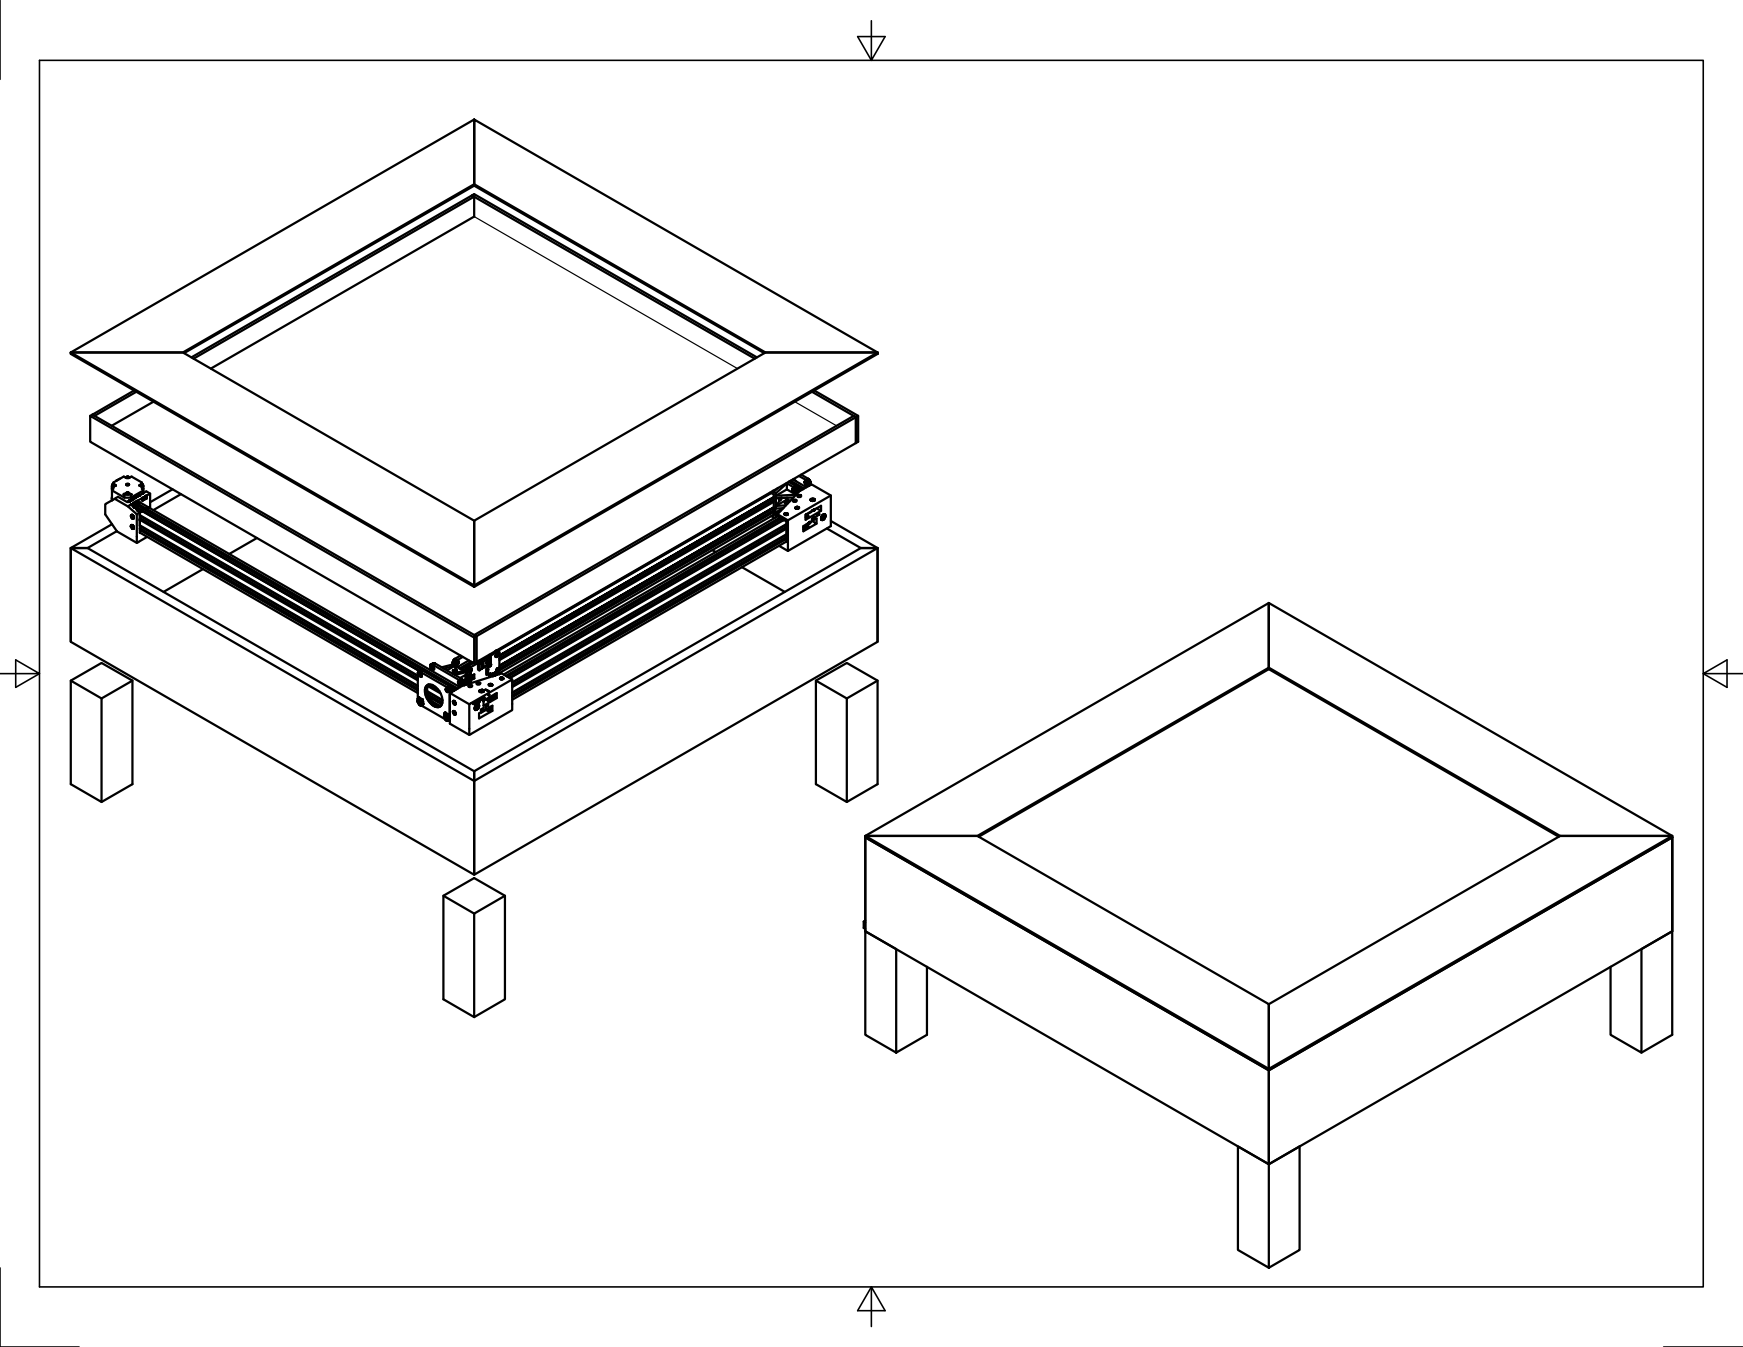
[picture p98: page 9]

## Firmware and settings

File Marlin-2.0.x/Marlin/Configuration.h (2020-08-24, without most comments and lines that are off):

#pragma once
#define CONFIGURATION_H_VERSION 020005
#define STRING_CONFIG_H_AUTHOR "(none, default config)" // Who made the changes.
#define SHOW_BOOTSCREEN
#define SERIAL_PORT 0
#define BAUDRATE 250000
  #define MOTHERBOARD BOARD_RAMPS_PLUS_EFB
#define EXTRUDERS 1
#define DEFAULT_NOMINAL_FILAMENT_DIA 3.0
#define TEMP_SENSOR_0 1
#define TEMP_SENSOR_1 0
#define TEMP_SENSOR_2 0
#define TEMP_SENSOR_3 0
#define TEMP_SENSOR_4 0
#define TEMP_SENSOR_5 0
#define TEMP_SENSOR_6 0
#define TEMP_SENSOR_7 0
#define TEMP_SENSOR_BED 0
#define TEMP_SENSOR_PROBE 0
#define TEMP_SENSOR_CHAMBER 0
#define DUMMY_THERMISTOR_998_VALUE 25
#define DUMMY_THERMISTOR_999_VALUE 100
#define MAX_REDUNDANT_TEMP_SENSOR_DIFF 10
#define TEMP_RESIDENCY_TIME     10  // (seconds) Time to wait for hotend to "settle" in M109
#define TEMP_WINDOW              1  // (°C) Temperature proximity for the "temperature reached" timer
#define TEMP_HYSTERESIS          3  // (°C) Temperature proximity considered "close enough" to the target
#define TEMP_BED_RESIDENCY_TIME 10  // (seconds) Time to wait for bed to "settle" in M190
#define TEMP_BED_WINDOW          1  // (°C) Temperature proximity for the "temperature reached" timer
#define TEMP_BED_HYSTERESIS      3  // (°C) Temperature proximity considered "close enough" to the target
#define HEATER_0_MINTEMP   5
#define HEATER_1_MINTEMP   5
#define HEATER_2_MINTEMP   5
#define HEATER_3_MINTEMP   5
#define HEATER_4_MINTEMP   5
#define HEATER_5_MINTEMP   5
#define HEATER_6_MINTEMP   5
#define HEATER_7_MINTEMP   5
#define BED_MINTEMP        5
#define HEATER_0_MAXTEMP 275
#define HEATER_1_MAXTEMP 275
#define HEATER_2_MAXTEMP 275
#define HEATER_3_MAXTEMP 275
#define HEATER_4_MAXTEMP 275
#define HEATER_5_MAXTEMP 275
#define HEATER_6_MAXTEMP 275
#define HEATER_7_MAXTEMP 275
#define BED_MAXTEMP      150
#define PIDTEMP
#define BANG_MAX 255     // Limits current to nozzle while in bang-bang mode; 255=full current
#define PID_MAX BANG_MAX // Limits current to nozzle while PID is active (see PID_FUNCTIONAL_RANGE below); 255=full current
#define PID_K1 0.95      // Smoothing factor within any PID loop
  #define PID_FUNCTIONAL_RANGE 10 // If the temperature difference between the target temperature and the actual temperature
  #define DEFAULT_Kp 22.2
  #define DEFAULT_Ki 1.08
  #define DEFAULT_Kd 114
#define MAX_BED_POWER 255 // limits duty cycle to bed; 255=full current
#define PREVENT_COLD_EXTRUSION
#define EXTRUDE_MINTEMP 170
#define PREVENT_LENGTHY_EXTRUDE
#define EXTRUDE_MAXLENGTH 200
#define THERMAL_PROTECTION_HOTENDS // Enable thermal protection for all extruders
#define THERMAL_PROTECTION_BED     // Enable thermal protection for the heated bed
#define THERMAL_PROTECTION_CHAMBER // Enable thermal protection for the heated chamber
#define COREYX
#define USE_XMIN_PLUG
#define USE_YMIN_PLUG
#define USE_ZMIN_PLUG
#define ENDSTOPPULLUPS
#define X_MIN_ENDSTOP_INVERTING false // Set to true to invert the logic of the endstop.
#define Y_MIN_ENDSTOP_INVERTING false // Set to true to invert the logic of the endstop.
#define Z_MIN_ENDSTOP_INVERTING false // Set to true to invert the logic of the endstop.
#define X_MAX_ENDSTOP_INVERTING false // Set to true to invert the logic of the endstop.
#define Y_MAX_ENDSTOP_INVERTING false // Set to true to invert the logic of the endstop.
#define Z_MAX_ENDSTOP_INVERTING false // Set to true to invert the logic of the endstop.
#define Z_MIN_PROBE_ENDSTOP_INVERTING false // Set to true to invert the logic of the probe.
#define X_DRIVER_TYPE  TMC2209
#define Y_DRIVER_TYPE  TMC2209
#define DEFAULT_AXIS_STEPS_PER_UNIT   { 200, 200, 4000, 500 }
#define DEFAULT_MAX_FEEDRATE          { 300, 300, 5, 25 }
#define DEFAULT_MAX_ACCELERATION      { 10000, 10000, 100, 10000 }
#define DEFAULT_ACCELERATION          10000    // X, Y, Z and E acceleration for printing moves
#define DEFAULT_RETRACT_ACCELERATION  10000    // E acceleration for retracts
#define DEFAULT_TRAVEL_ACCELERATION   10000    // X, Y, Z acceleration for travel (non printing) moves
#define DEFAULT_EJERK    5.0  // May be used by Linear Advance
  #define JUNCTION_DEVIATION_MM 0.013 // (mm) Distance from real junction edge
#define Z_MIN_PROBE_USES_Z_MIN_ENDSTOP_PIN
#define NOZZLE_TO_PROBE_OFFSET { 10, 10, 0 }
#define MIN_PROBE_EDGE 10
#define XY_PROBE_SPEED 8000
#define Z_PROBE_SPEED_FAST HOMING_FEEDRATE_Z
#define Z_PROBE_SPEED_SLOW (Z_PROBE_SPEED_FAST / 2)
#define Z_CLEARANCE_DEPLOY_PROBE   10 // Z Clearance for Deploy/Stow
#define Z_CLEARANCE_BETWEEN_PROBES  5 // Z Clearance between probe points
#define Z_CLEARANCE_MULTI_PROBE     5 // Z Clearance between multiple probes
#define Z_PROBE_LOW_POINT          -2 // Farthest distance below the trigger-point to go before stopping
#define Z_PROBE_OFFSET_RANGE_MIN -20
#define Z_PROBE_OFFSET_RANGE_MAX 20
#define X_ENABLE_ON 0
#define Y_ENABLE_ON 0
#define Z_ENABLE_ON 0
#define E_ENABLE_ON 0 // For all extruders
#define DISABLE_X false
#define DISABLE_Y false
#define DISABLE_Z false
#define DISABLE_E false             // For all extruders
#define DISABLE_INACTIVE_EXTRUDER   // Keep only the active extruder enabled
#define INVERT_X_DIR false
#define INVERT_Y_DIR true
#define INVERT_Z_DIR false
#define INVERT_E0_DIR false
#define INVERT_E1_DIR false
#define INVERT_E2_DIR false
#define INVERT_E3_DIR false
#define INVERT_E4_DIR false
#define INVERT_E5_DIR false
#define INVERT_E6_DIR false
#define INVERT_E7_DIR false
#define X_HOME_DIR -1
#define Y_HOME_DIR -1
#define Z_HOME_DIR -1
#define X_BED_SIZE 640
#define Y_BED_SIZE 633
#define X_MIN_POS 0
#define Y_MIN_POS 0
#define Z_MIN_POS 0
#define X_MAX_POS X_BED_SIZE
#define Y_MAX_POS Y_BED_SIZE
#define Z_MAX_POS 200
#define HOMING_FEEDRATE_XY (30*60)
#define HOMING_FEEDRATE_Z  (4*60)
#define EEPROM_CHITCHAT       // Give feedback on EEPROM commands. Disable to save PROGMEM.
#define EEPROM_BOOT_SILENT    // Keep M503 quiet and only give errors during first load
#define HOST_KEEPALIVE_FEATURE        // Disable this if your host doesn't like keepalive messages
#define DEFAULT_KEEPALIVE_INTERVAL 2  // Number of seconds between "busy" messages. Set with M113.
#define BUSY_WHILE_HEATING            // Some hosts require "busy" messages even during heating
#define PREHEAT_1_LABEL       "PLA"
#define PREHEAT_1_TEMP_HOTEND 180
#define PREHEAT_1_TEMP_BED     70
#define PREHEAT_1_FAN_SPEED     0 // Value from 0 to 255
#define PREHEAT_2_LABEL       "ABS"
#define PREHEAT_2_TEMP_HOTEND 240
#define PREHEAT_2_TEMP_BED    110
#define PREHEAT_2_FAN_SPEED     0 // Value from 0 to 255
#define PRINTJOB_TIMER_AUTOSTART
#define LCD_LANGUAGE en
#define DISPLAY_CHARSET_HD44780 JAPANESE
#define LCD_INFO_SCREEN_STYLE 0
#define SOFT_PWM_SCALE 0
#define SERVO_DELAY { 300 }

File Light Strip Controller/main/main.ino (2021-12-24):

#define FASTLED_ALLOW_INTERRUPTS 0
#include <FastLED.h>
#include "constants.h"
#include "mode.h"
#include "solidcolor.h"

CRGB leds[NUM_LEDS];

uint8_t mode = OFF; // Start with leds off
uint8_t *dat;

uint16_t millis_per_frame = 1e3 / 25;

void setup()
{
    delay(1000); // 1 second delay for recovery

    // tell FastLED about the LED strip configuration
    FastLED.addLeds<LED_TYPE, DATA_PIN, GRB>(leds, NUM_LEDS);

    // set master brightness control
    FastLED.setBrightness(BRIGHTNESS);
    FastLED.setMaxPowerInVoltsAndMilliamps(5, MAX_MILLIAMPS);

    // Set Serial baud rate
    Serial.begin(SERIAL_BAUD_RATE);

    // Initialize dat for the first time
    dat = init_dat(mode);
}

char inputBuf[BUF_SIZE];        // a String to hold incoming data
char cmd[BUF_SIZE];             // a String to hold the finished command
uint8_t buf_pos = 0;            // Current position in the buffer (and length of stored string)
bool newCommandReady = false;   // whether the string is complete
bool processingCommand = false; // a bool to prevent modifying cmd while reading it

void loop()
{
    // Compute next frame
    EVERY_N_MILLIS_I(thisTimer, millis_per_frame)
    {
        handle_serial_data();
        process_cmd();
        thisTimer.setPeriod(millis_per_frame);
        next_frame(mode, leds, dat);
        FastLED.show();
        // Serial.println(*dat);
    }
}

void process_cmd()
{
    // Check for new mode
    if (newCommandReady)
    {
        newCommandReady = false;
        processingCommand = true;

        // Verify start character
        if (cmd[0] == START_CHAR)
        {
            // Set new mode
            uint8_t newMode = (uint8_t)cmd[1];
            if (newMode != '\r' && newMode != '\n')
            {
                if (DEBUG)
                {
                    Serial.print("Setting new mode: ");
                    Serial.println(newMode);
                }

                if (newMode == BRIGHTNESS_CMD)
                {
                    // Check that the command is valid
                    if (cmd[3] == END_CHAR)
                    {
                        // Set new brightness
                        uint8_t b = cmd[2];

                        if (DEBUG)
                        {
                            Serial.print("Setting brightness: ");
                            Serial.println(b);
                        }

                        FastLED.setBrightness(b);

                        send_ack();
                    }
                }
                else if (newMode == FPS_CMD)
                {
                    // Check that the command is valid
                    if (cmd[3] == END_CHAR)
                    {
                        // Set new fps
                        uint16_t fps = cmd[2];
                        millis_per_frame = 1e3 / fps;

                        if (DEBUG)
                        {
                            Serial.print("Setting FPS: ");
                            Serial.println(fps);
                        }

                        send_ack();
                    }
                }
                else if (newMode == RGB_CMD)
                {
                    // Check that the command is valid
                    if (cmd[5] == END_CHAR)
                    {
                        // We are sending a solid color, not a predefined mode
                        // act accordingly...
                        uint8_t r = cmd[2];
                        uint8_t g = cmd[3];
                        uint8_t b = cmd[4];

                        if (DEBUG)
                        {
                            Serial.print("Setting solid color: (");
                            Serial.print(r);
                            Serial.print(", ");
                            Serial.print(g);
                            Serial.print(", ");
                            Serial.print(b);
                            Serial.println(")");
                        }

                        // Free old dat
                        free(dat);

                        // Init dat to solid color type
                        dat = init_solid_color_dat(r, g, b); // Assume rgb format

                        mode = SOLID_COLOR;

                        send_ack();
                    }
                }
                else
                {
                    // Check that the command is valid
                    if (cmd[2] == END_CHAR)
                    {
                        mode = newMode;

                        // Free old dat
                        free(dat);

                        // Init dat to correct type
                        dat = init_dat(mode);

                        send_ack();
                    }
                }
            }
        }

        processingCommand = false;
    }
}

void send_ack()
{
    Serial.println("ack");
}

void handle_serial_data()
{
    while (Serial.available())
    {
        // get the new byte:
        char inChar = (char)Serial.read();
        // if the incoming character is the start character, we are receiving the
        // beginning of a new command. Reset the buffer
        // Or, reset the buffer if we've filled it up.
        if (inChar == START_CHAR || buf_pos >= BUF_SIZE)
        {
            memset(inputBuf, 0, BUF_SIZE);
            buf_pos = 0;
        }

        inputBuf[buf_pos] = inChar;
        buf_pos++;

        // if the incoming character is the end character, set a flag so the
        // main loop can do something about it:
        if (inChar == END_CHAR)
        {
            // If we're processing a command already, just throw this new one away
            if (!processingCommand)
            {
                memcpy(cmd, inputBuf, BUF_SIZE);
                newCommandReady = true;
            }
            memset(inputBuf, 0, BUF_SIZE);
            buf_pos = 0;
        }
    }
}

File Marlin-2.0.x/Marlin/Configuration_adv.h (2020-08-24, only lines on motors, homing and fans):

#define E0_AUTO_FAN_PIN -1
#define E1_AUTO_FAN_PIN -1
#define E2_AUTO_FAN_PIN -1
#define E3_AUTO_FAN_PIN -1
#define E4_AUTO_FAN_PIN -1
#define E5_AUTO_FAN_PIN -1
#define CHAMBER_AUTO_FAN_PIN -1
#define X_HOME_BUMP_MM 0
#define Y_HOME_BUMP_MM 0
#define Z_HOME_BUMP_MM 2
#define HOMING_BUMP_DIVISOR { 2, 2, 4 }  // Re-Bump Speed Divisor (Divides the Homing Feedrate)
#define HOMING_BACKOFF_MM { 2, 2, 2 }  // (mm) Move away from the endstops after homing
#define HOME_Y_BEFORE_X
#define MICROSTEP_MODES { 16, 16, 16, 16, 16, 16 } // [1,2,4,8,16]
#define DIGIPOT_I2C_MOTOR_CURRENTS { 1.0, 1.0, 1.0, 1.0, 1.0, 1.0, 1.0, 1.0 }  //  AZTEEG_X3_PRO
    #define X_CURRENT       800        // (mA) RMS current. Multiply by 1.414 for peak current.
    #define X_CURRENT_HOME  400  // (mA) RMS current for sensorless homing
    #define X_MICROSTEPS     32    // 0..256
    #define Y_CURRENT       800
    #define Y_CURRENT_HOME  400
    #define Y_MICROSTEPS     32
  #define X_HYBRID_THRESHOLD     100  // [mm/s]
  #define X2_HYBRID_THRESHOLD    100
  #define Y_HYBRID_THRESHOLD     100
  #define Y2_HYBRID_THRESHOLD    100
  #define Z_HYBRID_THRESHOLD       3
  #define Z2_HYBRID_THRESHOLD      3
  #define Z3_HYBRID_THRESHOLD      3
  #define Z4_HYBRID_THRESHOLD      3
  #define E0_HYBRID_THRESHOLD     30
  #define E1_HYBRID_THRESHOLD     30
  #define E2_HYBRID_THRESHOLD     30
  #define E3_HYBRID_THRESHOLD     30
  #define E4_HYBRID_THRESHOLD     30
  #define E5_HYBRID_THRESHOLD     30
  #define E6_HYBRID_THRESHOLD     30
  #define E7_HYBRID_THRESHOLD     30
  #define SENSORLESS_HOMING // StallGuard capable drivers only
    #define X_STALL_SENSITIVITY  40
    #define X2_STALL_SENSITIVITY X_STALL_SENSITIVITY
    #define Y_STALL_SENSITIVITY  20
    #define IMPROVE_HOMING_RELIABILITY

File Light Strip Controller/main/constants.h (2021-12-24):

#ifndef LIGHT_STRIP_CONTROLLER_CONSTANTS_H

#define LIGHT_STRIP_CONTROLLER_CONSTANTS_H

// General Constants
#define DEBUG false
#define SERIAL_BAUD_RATE 115200
#define BUF_SIZE 32

// Communication Protocol Constants
#define START_CHAR '['
#define END_CHAR ']'
#define BRIGHTNESS_CMD '!'
#define FPS_CMD '@'
#define RGB_CMD '#'

// LED Strip Constants
#define DATA_PIN 3
#define LED_TYPE WS2813
#define NUM_LEDS 240
#define BRIGHTNESS 255
#define MAX_MILLIAMPS 12000

// Color Modes
#define OFF 0
#define RAINBOW 1
#define CHRISTMAS 2
#define COLOR_PULSE 3
#define AMBIANCE 4
#define CONFETTI 5

#define SOLID_COLOR 255 // Not to be used by client...only internally

// Color Pulse Mode Constants
#define PULSE_FREQUENCY 3               // Frequency for a new pulse in Hz  \
                                        // Will be on average this value... \
                                        // actual pulses will be created using rng
#define PULSE_MIN_SATURATION 225        // Out of 255
#define PULSE_INTENSITY 50              // bigger the number, longer the leds stay bright, 0 is no change
#define PULSE_BACKGROUND_BRIGHTNESS 80  // 0..255

// Ambiance Mode Constants
#define AMBIANCE_SATURATION 100
#define AMBIANCE_CHANGE_RATE 0.03 // Defines the bounds for the random walk
#define AMBIANCE_MAX_CHANGE_RATE 0.3

// Confetti Mode Constants
#define CONFETTI_DECAY_RATE 2 // Low values = slower fade
#define CONFETTI_SATURATION 150


#endif

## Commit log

2020-08-25 updated marlin readme
2020-08-29 fixed bug where sliding brightness slider crashes led strip controller also updated light strip controller readme
2020-08-31 updated readme, added bom spreadsheet
    [sand_table_bom.xlsx]
2020-09-02 added hardware guide and stls
    [1-HbarEndLeft.stl, 1-HbarEndRight.stl, 1-MagnetClamp.stl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]
2020-09-03 optimization in track image generation: - generating filled preview is unnecessary - instead, scale the standard preview by sqrt(2)
2020-09-03 Some fixes related to running on a raspberry pi
2020-11-24 Added M5 10mm bolts to BOM
    For some reason they weren't there before, so that should be fixed now
    [sand_table_bom.xlsx]
2020-11-29 added counterbore to holes
    A few screw holes were too deep for the short 10mm M5 screws to pass through. A counterbore has been added so that these screws can sit further inside the part.
    [1-MotorMountLeft.stl, 1-MotorMountRight.stl, 1-RearIdlerLeft.stl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]
2020-12-23 added multithreading/process support - gcode_controller runs on a separate child process now - create_png_from_gcode and _process_theta_rho run on their own threads when called - this is to fix issue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
    [constants.h]
2021-01-14 Changed stl units to mm
    Previously, stl units were in inches, which caused scaling issues when importing into a slicer like Cura.
    This should be fixed now.
    [1-HbarEndLeft.stl, 1-HbarEndRight.stl, 1-MagnetClamp.stl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]
2021-03-08 added steps for identifying serial ports of usb devices connected to the Pi
2021-12-24 Improved led strip controller - Faster communication between server and controller - More robust protocol with start/end characters - Update rate from client to led strip ~10x faster - Ack sent from 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
2023-01-21 Redesigned wheel spacer to have a lip at the bearing interface
    [24-WheelSpacer.stl]
2023-01-21 Updated build guide to reflect wheel spacer redesign
2023-01-22 Improved and unified print carriage STL; Added STL for use with heat-set inserts
    [1-PrintCarriageFront.stl, 1-PrintCarriageRear.stl, 2-PrintCarriage.stl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]
2023-01-22 Unified HBAR designs
    [1-HbarEndRight.stl, 2-HbarEnd.stl]
2023-01-23 Increased diameter of HSI holes to 4.25
    [2-PrintCarriageFront_HeatSetInserts.stl]
2023-01-31 Provided alternate rear idlers
    [1-RearIdlerLeft_NoRearBar.stl, 1-RearIdlerRight_NoRearBar.stl]
2024-12-28 Fix bug where website crashes when sending LED commands

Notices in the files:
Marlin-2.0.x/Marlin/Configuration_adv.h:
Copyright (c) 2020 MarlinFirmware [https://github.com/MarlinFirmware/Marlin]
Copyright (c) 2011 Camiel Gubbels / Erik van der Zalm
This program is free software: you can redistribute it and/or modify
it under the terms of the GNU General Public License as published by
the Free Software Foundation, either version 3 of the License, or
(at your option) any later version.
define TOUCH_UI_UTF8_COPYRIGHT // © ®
